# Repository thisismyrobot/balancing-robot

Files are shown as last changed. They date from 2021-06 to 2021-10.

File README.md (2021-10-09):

# Balancing robot

Using a BetaFlight-equipped flight controller (and later on an MPU6050) to
give the orientation and an Arduino Nano (and later an ESP32) for control.

End goal is the Wheelie Boy from The Peripheral.

This is an educational (for myself) project but I want to share my steps
towards achieving (or not) this goal.

If you want to try out some of the code, use the tags below, anything else is
probably WIP and may not do anything useful :)

## Version 4 (TODO/WIP)

### Thoughts

 * Will build a new chassis, with new motors, and target wheel size.
 * If encoders are high enough resolution I will retry the closed-loop
   control, if not will instead use the behaviour (ie oscillating, running
   away) to self tune a little.
 * Will move control board to bottom to simplify wiring and to stop instances
   where I tap the "head" back and forward while tuning from saturating the
   accelerometers which caused it to lose an accurate "zero" inclination.
 * Definitely using an MPU6050.

## Version 3

See [Tag 3.0](https://github.com/thisismyrobot/balancing-robot/releases/tag/3.0)

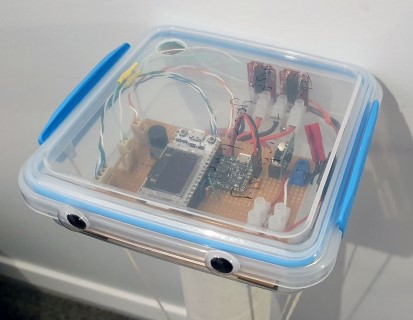
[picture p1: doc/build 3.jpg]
 

### Hardware

 * HappyModel SP Racing F3 EVO Brushed Micro FC - running BetaFlight 3.1.7 with minimal configuration except for fast serial response.
 * 2 x Solarbotics L293D Secret Motor Driver
 * Heltec Automation WiFi Kit 32 (an ESP32 board) for control
 * ~~2 x DG01D-E 48:1 DC motor w/wheel, 3-9V~~ 2 x 48.75:1 DC motor w/wheel, 3-12V (search for "Arduino DC Motor with Wheel and Rubber Tyres") + bodged-on encoders from DG01D-E, as the DG01D-E is just not powerful enough. Measurements suggest 1/3 of the power.
 * Pololu 5V, 2.5A Step-Down Voltage Regulator D24V22F5
 * 3S LiPo (450mAh 45C)

### Thoughts

Not a great success. Switching to an ESP32 was a good, but implementing
closed-loop motor control didn't improve motor speed accuracy as the encoder
counts per revolution were too low. As a consequence a slower PID loop
frequency was needed to ensure enough counts were taken to correct the speed,
but that introduced lag in response.

## Version 2

See [Tag 2.0](https://github.com/thisismyrobot/balancing-robot/releases/tag/2.0)

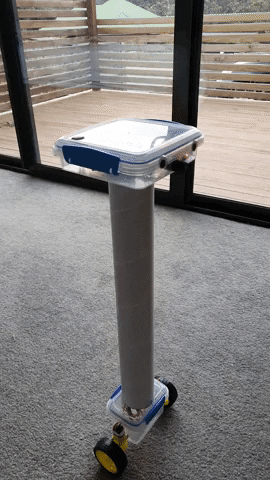
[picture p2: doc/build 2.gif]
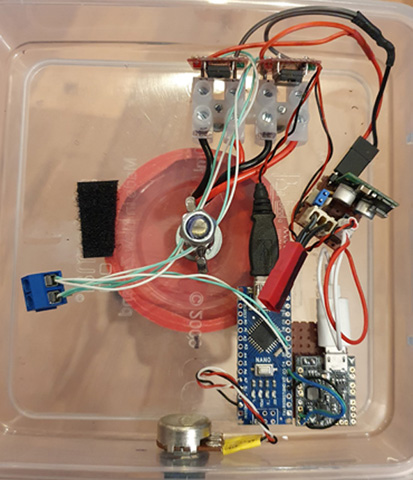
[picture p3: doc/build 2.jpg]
 

### Hardware

 * HappyModel SP Racing F3 EVO Brushed Micro FC - running BetaFlight 3.1.7
  with minimal configuration except for fast serial response.
 * 2 x Solarbotics L293D Secret Motor Driver
 * Arduino Nano
 * 2 x 48.75:1 DC motor w/wheel, 3-12V (search for "Arduino DC Motor with
   Wheel and Rubber Tyres")
 * Pololu 5V, 2.5A Step-Down Voltage Regulator D24V22F5
 * 3S LiPo (450mAh 45C)

### Thoughts

Pretty much balances. Next version will use encoders to get better motor speed
control and also distance measurement so I can start correcting for it
creeping.

## Version 1

See [Tag 1.0](https://github.com/thisismyrobot/balancing-robot/releases/tag/1.0)

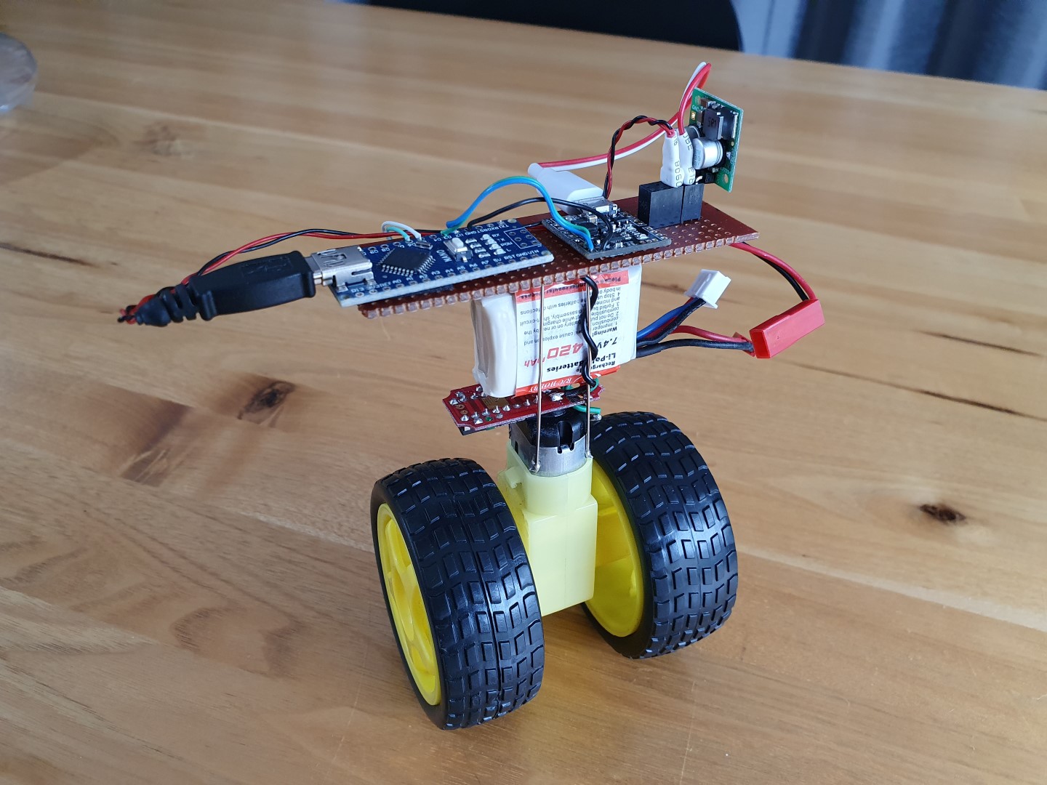
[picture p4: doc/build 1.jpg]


### Hardware

 * HappyModel SP Racing F3 EVO Brushed Micro FC - running BetaFlight 3.1.7
   with minimal configuration.
 * Solarbotics L293D Secret Motor Driver
 * Arduino Nano
 * 48.75:1 DC motor w/wheel, 3-12V (search for "Arduino DC Motor with Wheel
   and Rubber Tyres")
 * Pololu 5V, 2.5A Step-Down Voltage Regulator D24V22F5
 * 2S and 3S LiPos to test (3S better)

### Thoughts

Too short to even start tuning PID, but it was a good proof of concept of
using the drone controller for orientation.

# Some notes on motors

I am trying different motors as I progress and I'll log what I know about them
here, performance-wise.

| Motor model | Robot version(s) | Stall Torque | No Load Speed |
| --- | --- | --- | --- |
| DG01D-A130GEARMOTOR | 1 + 2 | 0.8kg/cm @ 4.5V | 180 RPM @ 4.5V |
| DG01D-E | 3? | 0.8kg/cm @ 4.5V | 180 RPM @ 4.5V |
| FS90R | 4? Wheelie Boy? | 1.3kg/cm @ 4.8V | 100 RPM @ 4.8V |

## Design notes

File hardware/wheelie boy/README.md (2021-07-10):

# Notes as I spec out the wheelie boy design from The Peripheral

https://app.milanote.com/1LZwqI1BNqTP8V?p=4gEVYU8Zxy4

## Font

Font is ToySans from: https://www.fontspace.com/category/toys-r-us

    license: Creative Commons (by-nc-nd) Attribution Non-commercial No Derivatives 
    link: https://www.fontspace.com/toysans-font-f22064

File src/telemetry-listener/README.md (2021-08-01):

# Telemetry Listener

Prints out telemetry from the robot, received over UDP.

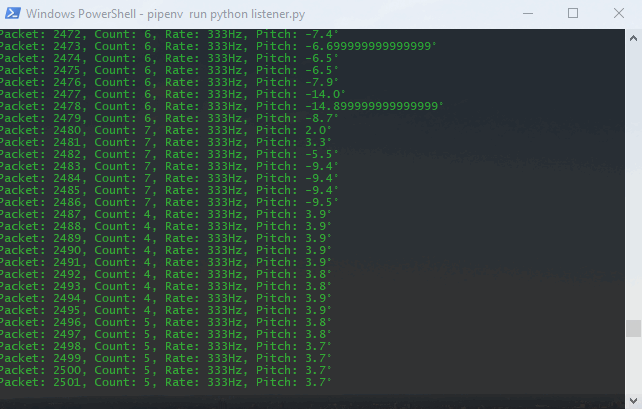
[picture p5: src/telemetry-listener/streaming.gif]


## PID tuning

An example application is the closed-loop motor control tuning I did using
data from the listener:

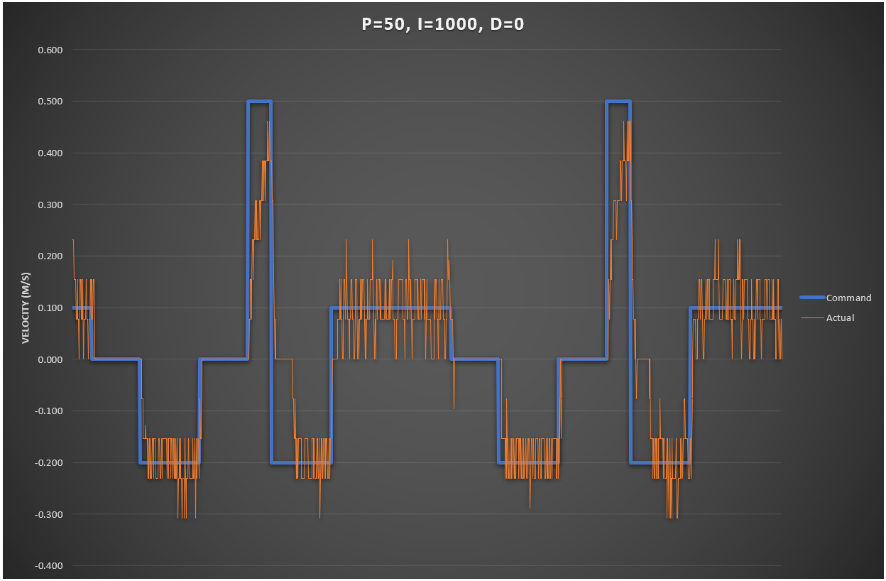
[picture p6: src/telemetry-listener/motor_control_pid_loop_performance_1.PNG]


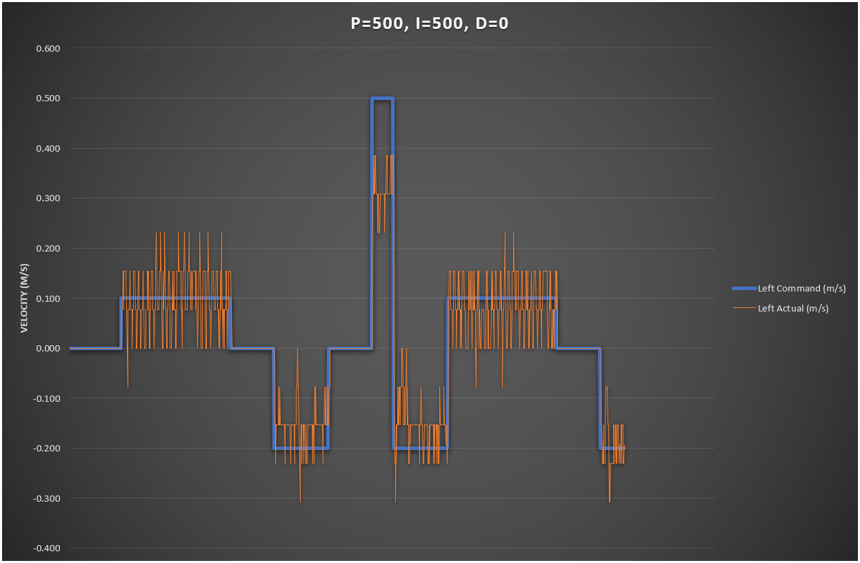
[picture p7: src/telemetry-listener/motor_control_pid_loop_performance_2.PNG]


## Install

    pip install pipenv
    pipenv install

## Run

    pipenv run python listener.py

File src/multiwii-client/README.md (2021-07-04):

Simple Python client to stream attitude data from a MultiWii serial device.

Built to find out how fast I could request data.

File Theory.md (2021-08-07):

# What (I think) makes a good balancing robot

Trying to describe this without a formula. It's close to correct but I will
keep updating as I learn more.

## Height/centre of mass/moment of inertia

Moving and concentrating mass towards the top of the robot will give the
control system more time to react to tipping and reduce the power requirements
of the motors to regain balance.

### Centre of Mass

The Centre of Mass of an object is the average position of the items within
it, weighted by their mass.

For the purposes of approximation, the Centre of Mass of our robot is it's
balance point along its length when laying on it's side.

## Torque Arm

When a solid object has a force put upon it, and that force is not directly
pointing at the Centre of Mass, the object will both move and be torqued
around the Centre of Mass. The line from the Centre of Mass to where the force
is acting is the Torque Arm. The longer the Torque Arm the greater the torque.
The greater the angle between the Torque Arm and the force, the more the force
will contribute to rotation and less to moving. 100% of the force will
contribute to rotation when the force is acting at 90 degrees to the Torque
Arm.

### Moment of Inertia

The Moment of Inertia of an object is its resistance to acceleration around a
pivot, based on its mass and the distribution of its mass compared to the
pivot. Adding mass to an object or moving an object's mass away from a pivot
will both increase the Moment of Inertia.

The greater the Moment of Inertia a mass has around a pivot, the more
resistant it will be to forces trying to accelerate its rotation around around
that pivot.

## Tipping

When the robot is stationary and starting to tip, it is because gravity is
applying a vertical force that is resulting in a torque around a pivot (its
wheel contact patches). The higher the Moment of Inertia is around the pivot,
the more slowly it will accelerate in rotation towards the ground.

The benefit of it more slowly accelerating is your control system has more
time to correct.

## Recovering

When a robot moves laterally to correct its balance, two forces are in play.

Firstly, the rotation of the wheels by the motor creates an opposite torque on
the robot that attempts to straighten it. The lighter the robot the more
impact this torque will have. The greater the Moment of Inertia of the robot
around the axle pivot, the less impact the torque will have.

This torque is not generally accounted for in your control system so the less
impact it has the better.

Secondly, the sideways motion of the base of the robot as it attempts to move
the wheels directly under the top is a lateral force on the bottom of the
robot that is attempting to torque the robot to vertical. The Torque Arm is
between the Centre of Mass and the wheel contact patches. Inhibiting this
torque will be the Moment of Inertia of that rotation around the Centre of
Mass. The higher up the robot the centre of mass is and/or the more
concentrated it is at the Centre of Mass (and thus the lower the Moment of
Inertia around the Centre of Mass pivot), the the less lateral force required
to torque the robot back to vertical.

This reduction in required lateral force reduces the power requirements of the
motors.

# Tuning approach

The usual, tune P, the I, then D. Some people say for balancing robots to go
with zero I, some go with I = 10x P. YMMV. D is nearly always a 100th or
1000th of P.

# Fast PID control loop time

I got now meaningful balancing performance before hitting over 150Hz loop
time (currently 192 Hz). At 10Hz it was hopeless.

I don't have a good external reference but 1ms loop times (so 1000Hz) are
successful in https://www.youtube.com/watch?v=TN6u-D992sw

# Constant PID control loop time

Using the standard Arduino PID library, variances in PID control loop time are
not taken into account which can impact D term. Keep it as constant as
possible.

# Battery voltage vs. P

Consider raising P by the drop (%) in battery voltage, and vice versa. Motor
voltage is proportional to motor speed so this will help maintain level
performance as a battery sags.

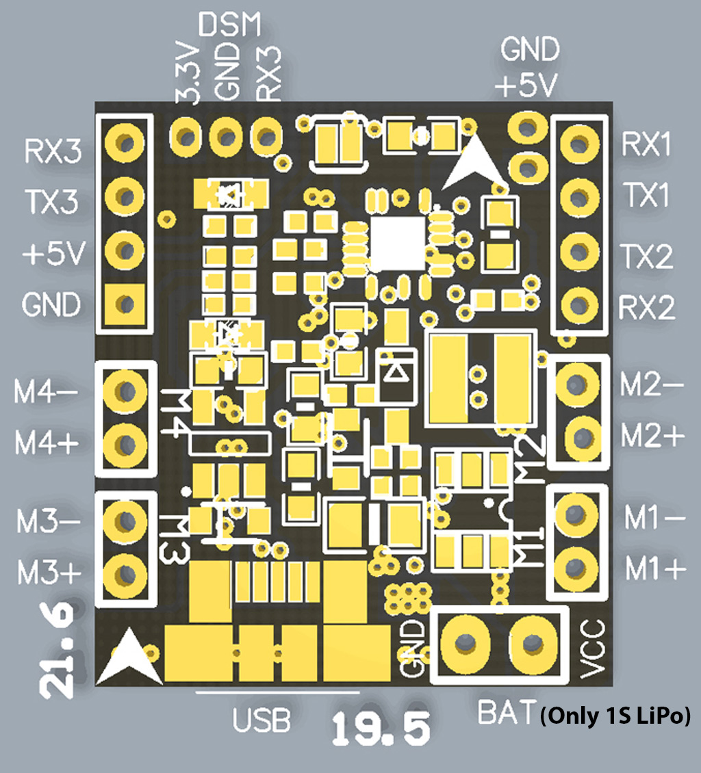
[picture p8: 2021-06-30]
hardware/HappyModel SP Racing F3 EVO Brushed Micro FC/happymodel-f3-evo-brushed-v2-big001.jpg

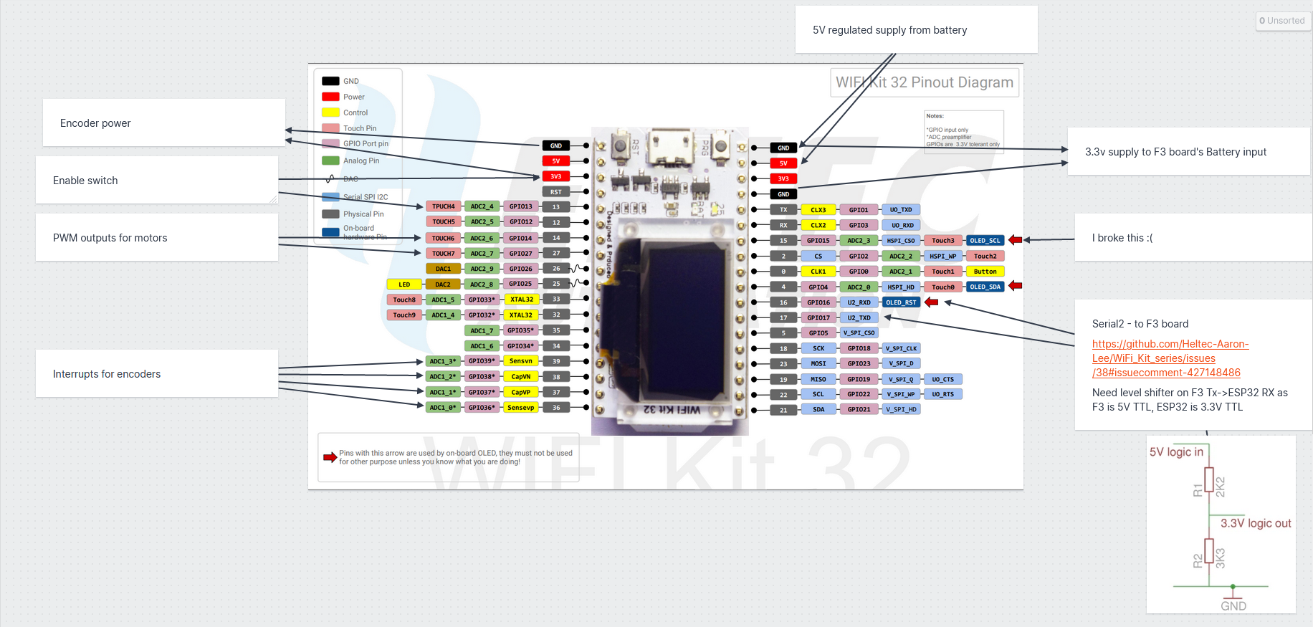
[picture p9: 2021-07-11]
hardware/Heltec WiFi Kit 32/Integration.PNG

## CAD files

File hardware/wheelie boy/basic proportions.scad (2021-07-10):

$fn = 50;

module rod(diameter, height) {
    color([1, 0, 0]) cylinder(h=height, r=diameter / 2);
}

module base(diameter) {
    color([1, 0, 0]) sphere(r=diameter / 2);
}

module screen(width, height, thickness) {
    color([0, 0, 0]) translate([-thickness / 2, -width / 2, 0]) cube([thickness, width, height]);
}

module wheel(width, diameter) {
    
    translate([0, 0, -width * 0.125]) cylinder(h=width * 0.25, r=(diameter / 2) - width);
    color([0.2, 0.2, 0.2]) rotate_extrude() translate([(diameter / 2) - (width / 2), 0, 0]) circle(r = width / 2);
}

ball_diam = 10;
rod_height = 35;
rod_diam = 1;

screen_height = ball_diam * 2;
screen_width = screen_height * (3/4);

base(ball_diam);
translate([0, 0, ball_diam / 2]) rod(rod_diam, rod_height);
translate([0, 0, rod_height + (ball_diam / 2)]) screen(screen_width, screen_height, 1);
translate([0, (ball_diam / 2)+1.5, 0]) rotate([-90, 0, 0]) wheel(ball_diam / 2.5, ball_diam * 1.2);
translate([0, -(ball_diam / 2)-1.5, 0]) rotate([90, 0, 0]) wheel(ball_diam / 2.5, ball_diam * 1.2);

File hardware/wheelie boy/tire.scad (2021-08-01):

use <Toysans-Xe5d.ttf>

print = false;

$fn = print ? 200 : 20;

hub_width = 26;
hub_diam = 51.6;

hubcap_thickness = 1;

spoke_width = 0.75; // Tune to single pass of nozzle.

rim_width = 2;
tire_diam = 110;
tire_width = 30;
    

module hub()
{
    cylinder(r=hub_diam / 2, h=hub_width);
}

module hubCap()
{
    color([0.5, 0.5, 0.5]) cylinder(r=hub_diam / 2, h=hubcap_thickness);
    
    font_size = hub_diam / 6;
    translate([0, 0, hubcap_thickness]) linear_extrude(hubcap_thickness) text("Wheelie", font_size, "ToySans", halign="center", spacing=1.1);    
    translate([0, -hub_diam / 4.5, hubcap_thickness]) linear_extrude(hubcap_thickness) text("Boy", font_size, "ToySans", halign="center", spacing = 1.1);    
}

module tire()
{
    // Inner rim.
    difference() {
        cylinder(r=(hub_diam / 2) + rim_width, h=tire_width);
        translate([0, 0, -10]) cylinder(r=hub_diam / 2, h=tire_width + 20);
    }

    // Inner rim.
    difference() {
        cylinder(r=(tire_diam / 2), h=tire_width);
        translate([0, 0, -10]) cylinder(r=(tire_diam / 2) - rim_width, h=tire_width + 20);
    }
   
    // Airless-ness (think Michelin "Uptis")
    length = ((tire_diam - hub_diam) / 2) - (rim_width * 1.5);
    spokes = 30;
    for ( i = [0 : spokes] )
    {
        rotate([0, 0, (360 / spokes) * i]) translate([(hub_diam / 2) + rim_width, 0, 0]) linear_extrude(tire_width) {
            polygon(points=[[-rim_width/2,-spoke_width/2],[length,-spoke_width/2],[length,spoke_width/2],[-rim_width/2,spoke_width/2]]);
        }
    }
}

if (!print) {
    hub();
    translate([0, 0, hub_width]) hubCap();
}
else {
    translate([0, ((tire_diam + hub_diam) / 2) + 10, 0]) hubCap();
}

color([0.5, 0.5, 0.5]) tire();

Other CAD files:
hardware/wheelie boy/old artwork/WheelieBoy.skp

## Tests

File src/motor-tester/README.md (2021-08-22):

# Some DC motor theory

For a DC motor receiving a rated voltage:

 - It will have a Stall Torque, and a rated (no-load) RPM
 - Torque reduces linearly from the Stall Torque at zero RPM to zero at the rated RPM
 - The peak power is at 1/2 of the Stall Torque - which is the same point as half the rated RPM

https://nrsyed.com/2018/01/21/how-to-read-a-dc-motor-datasheet/

That means you can estimate peak power by calculating the power with inputs of
1/2 the Stall Torque and 1/2 the rated no-load RPM.

## Units/constants

### f<sub>RPM</sub>

This is not a real unit, but I'm using it to make the formulas clearer to
understand - it is the RPM of the motor.

### P = Power (Watts)

### τ = Torque (Nm)

Can be calculated from kgf.cm using: τ = (kgf.cm * g) / 100

Can be converted to kgf.cm using: kgf.cm = (τ * 100) / g

### ω = Angular Velocity (Radians/second)

Can be calculated from RPM using: ω = 2π * (f<sub>RPM</sub> / 60)

### g = Gravity

9.80665

## Formulas

### P = τ * ω

Power from torque and angular velocity

### Estimated power

Populating from above components:

P = (τ<sub>stall</sub> / 2) * ((2π * (f<sub>RPM</sub> / 60)) / 2)

Simplified:

P = (π * f<sub>RPM</sub> * τ<sub>stall</sub>) / 120

#### Example

https://www.banggood.com/CHIHAI-MOTOR-DC12V-350rpm-Encoder-Motor-DC-Gear-Motor-with-Cover-p-1245484.html

Motor rated speed (f<sub>RPM</sub>): 11907rpm (after 34.02:1 gearbox)
Blocking (stall) torque (τ<sub>stall</sub>): 12kg.cm (which after 34.02:1 gearbox is 0.03459 Nm)

P = (π * f<sub>RPM</sub> * τ<sub>stall</sub>) / 120

  = (π * 11907 * 0.03459) / 120

  = 10.7 Watts @ 12V @ 5954 RPM

As compared to 8.5W on document?

## Experiments in measuring comparable motor performance

###  stall_torque_calculator.py - measuring stall torque per volt

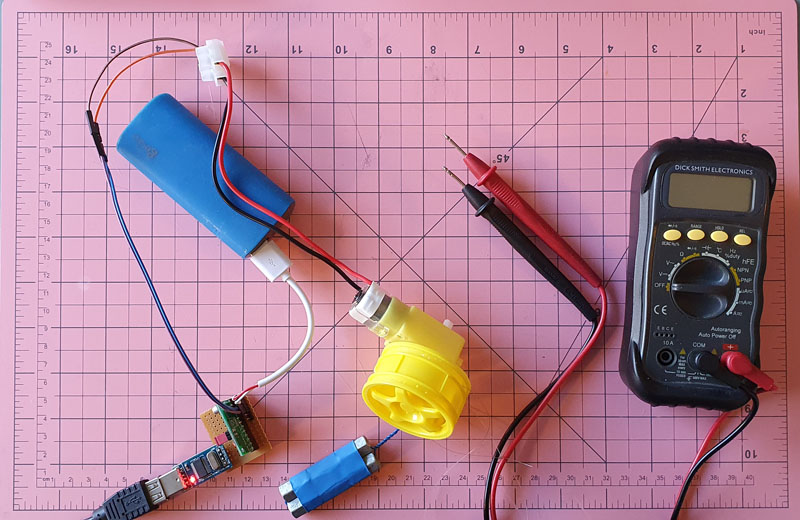
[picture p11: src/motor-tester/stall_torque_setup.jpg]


The idea is to ramp voltage until a weight starts to lift, then slow down
until it stops lifting, measure the voltage and use the mass and lifting wheel
diameter to determine the applied torque when it stalled.

Stall torque increases with voltage, fairly linearly, so we can apply the
ratio of the stall torque and voltage to estimate a stall torque per a spec
sheet volt value to compare motors by even if the voltage at which their stall
torque is specified at differs.

#### DG01D-A130GEARMOTOR

This motor + gearbox is spec'd to be 0.8kgf.cm @ 4.5V. As a ratio that is
0.17778 kgf.cm/V.

pipenv run python stall_torque_calculator.py --qik

    Mass of weight in kilograms (0.052):
    Wheel diameter in metres (0.0479):
    Supply voltage (5): 5.1
    Press [Enter] to begin...
    Press [Enter] when the motor starts!
    Press [Enter] when the motor stops!
    0.01Nm (0.12kgf.cm) @ 0.92V => 0.01328Nm/V (0.1354kgf.cm/V)

This is quite different to spec, but I think that the voltage was too far away
from the nominal, and more weight seems to improve the accuracy:

pipenv run python stall_torque_calculator.py --qik

    Mass of weight in kilograms (0.052): 0.16
    Wheel diameter in metres (0.0479):
    Supply voltage (5): 5.1
    Press [Enter] to begin...
    Press [Enter] when the motor starts!
    Press [Enter] when the motor stops!
    0.04Nm (0.38kgf.cm) @ 2.00V => 0.01879Nm/V (0.1916kgf.cm/V)

pipenv run python stall_torque_calculator.py --qik

    Mass of weight in kilograms (0.052): 0.284
    Wheel diameter in metres (0.0479):
    Supply voltage (5): 5.1
    Press [Enter] to begin...
    Press [Enter] when the motor starts!
    Press [Enter] when the motor stops!
    0.07Nm (0.68kgf.cm) @ 3.44V => 0.01939Nm/V (0.1977kgf.cm/V)

These two results are very close, despite a (~75% increase in weight), and
their average (0.19465) is pretty accurate, because 0.19465 * 4.5V =
0.875925kgf.cm and, as above, the spec says the stall torque is 0.8kgf.cm at
4.5V for this motor.

I think there is potential in this technique of estimating comparable stall
torque between different tested motors and spec sheets, as long as the stall
voltages are reasonable close.

#### DG01D-E

pipenv run python stall_torque_calculator.py --qik

    Mass of weight in kilograms (0.052):
    Wheel diameter in metres (0.0479):
    Supply voltage (5): 5.1
    Press [Enter] to begin...
    Press [Enter] when the motor starts!
    Press [Enter] when the motor stops!
    0.01Nm (0.12kgf.cm) @ 1.88V => 0.00650Nm/V (0.0662kgf.cm/V)

pipenv run python stall_torque_calculator.py --qik

    Mass of weight in kilograms (0.052): 0.09
    Wheel diameter in metres (0.0479):
    Supply voltage (5): 5.1
    Press [Enter] to begin...
    Press [Enter] when the motor starts!
    Press [Enter] when the motor stops!
    0.02Nm (0.22kgf.cm) @ 2.68V => 0.00789Nm/V (0.0804kgf.cm/V)

pipenv run python stall_torque_calculator.py --qik

    Mass of weight in kilograms (0.052): 0.162
    Wheel diameter in metres (0.0479):
    Supply voltage (5): 5.1
    Press [Enter] to begin...
    Press [Enter] when the motor starts!
    Press [Enter] when the motor stops!
    0.04Nm (0.39kgf.cm) @ 4.18V => 0.00910Nm/V (0.0928kgf.cm/V)

This backed up some of the results I had before, though the motor is soo weak
I had to use lower weights. On pure comparison though, the DG01D-E is has a
50% lower stall torque compared to the DG01D-A130GEARMOTOR. The below
measurements show it as having 1/3 of the power. No wonder it's not working
for V3 of this robot.

### tester.py - measuring motor power

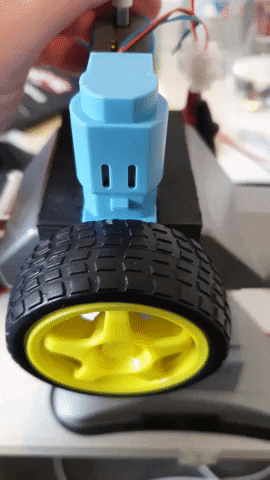
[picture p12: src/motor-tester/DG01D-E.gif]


This is a little simpler. By lifting a known weight a known distance over a
known time, using a known voltage, you can calculate the power in Watts of a
motor.

#### DG01D-A130GEARMOTOR

py tester.py

    Mass of weight in kilograms (0.05):
    Wheel diameter in metres (0.0665):
    Wheel rotations (2):
    Duration of lift in seconds: 0.65
    Battery voltage (5):
    0.02Nm (0.17kgf.cm) & 0.32W @ 5.0V & 184.62RPM

#### DG01D-E

py tester.py

    Mass of weight in kilograms (0.05):
    Wheel diameter in metres (0.0665):
    Wheel rotations (2): 1
    Duration of lift in seconds: 0.9666666666666667
    Battery voltage (5):
    0.02Nm (0.17kgf.cm) & 0.11W @ 5.0V & 62.07RPM

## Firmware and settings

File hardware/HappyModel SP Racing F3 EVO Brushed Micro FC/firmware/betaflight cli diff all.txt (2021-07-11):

# diff all
# Betaflight / SPRACINGF3EVO 3.1.7 Apr  3 2017 / 22:28:08 (e1c4b5c)
defaults

feature -VBAT
feature -CURRENT_METER
feature -RSSI_ADC
feature -BLACKBOX
feature -TRANSPONDER
feature -SDCARD
feature SOFTSERIAL
serial 0 1 115200 57600 0 115200
set serial_update_rate_hz = 1000
profile 0

rateprofile 0
rateprofile 0

rateprofile 1

rateprofile 2

rateprofile 0
profile 1

rateprofile 0
rateprofile 0

rateprofile 1

rateprofile 2

rateprofile 0
profile 2

rateprofile 0
rateprofile 0

rateprofile 1

rateprofile 2

rateprofile 0
profile 0
save

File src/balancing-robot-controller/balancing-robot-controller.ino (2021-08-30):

/*
 * Add https://dl.espressif.com/dl/package_esp32_index.json as an additional board manager URL.
 * Install esp32 board via the board manager (1.0.6).
 * Select Heltec_Wifi_Kit_32 as board.
 * 
 * Extra libraries:
 *  - MsgPack (0.3.8)
 *  - PID (1.2.0)
 *  - ESP32Encoder (0.5.1)
 * 
 */
#include <Arduino.h>
#include <HardwareSerial.h>
#include <PID_v1.h>
#include "src/telemetry.h"
#include "src/configuration.h"
#include "src/drive.h"

// Robot configuration and characteristics.
#define ANGLE_DEADZONE 0.1 // +/- this pitch value is considered zero.
#define ANGLE_FALLEN 40

// Closed loop motor control.
#define WHEEL_DISTANCE_M 0.208916  // 66.5mm diameter.
#define ENC_PULSES_PER_ROTATION 543.0  // 48:1 gearbox and ?!?! 11.3125 divisor. Odd.
#define MOTOR_CONTROL_P 50
#define MOTOR_CONTROL_I 1000
#define MOTOR_CONTROL_D 0

// Arduino wiring configuration.
#define ENABLE_GPIO 13
#define LED_GPIO 25

#define MOTOR_FORWARD_LEFT_GPIO 27
#define MOTOR_REVERSE_LEFT_GPIO 14
#define MOTOR_FORWARD_RIGHT_GPIO 26
#define MOTOR_REVERSE_RIGHT_GPIO 25

#define ENC_LEFT_A_GPIO 39
#define ENC_LEFT_B_GPIO 38
#define ENC_RIGHT_A_GPIO 36
#define ENC_RIGHT_B_GPIO 37

// PWM
#define PWM_FREQUENCY 5000
#define PWM_RESOLUTION 8
#define PWM_MOTOR_FORWARD_LEFT_CHANNEL 0
#define PWM_MOTOR_REVERSE_LEFT_CHANNEL 1
#define PWM_MOTOR_FORWARD_RIGHT_CHANNEL 2
#define PWM_MOTOR_REVERSE_RIGHT_CHANNEL 3

// Multi-Wii commands.
#define MSP_ATTITUDE 108

// PID configuration.
#define P 0.1
#define I 0.0
#define D 0.0

// PID instances.
double pitchPidSetpoint = 0;
double pitchPidInput;
double pitchPidOutput;
PID pitchPid(&pitchPidInput, &pitchPidOutput, &pitchPidSetpoint, P, I, D, DIRECT);

// Motor commands and tracking
double leftSpeedCommand = 0;
double rightSpeedCommand = 0;
double leftSpeedActual = 0;
double rightSpeedActual = 0;

// Statistics/telemetry
int watchdog = 0;
int rate = 0;
const int statsUpdateMillis = 250;
unsigned long lastStatsUpdateMillis = 0;
int rateLoops = 0;

// Subtracted from sensor reading to get robot balanced = 0.
double pitchCorrection = 0;

// Pointers to the shared data for telemetry and configuration.
TelemetryData_t telemetryData = {
    &watchdog,
    &rate,
    &pitchCorrection,
    &pitchPidInput,
    &pitchPidOutput,
    &leftSpeedCommand,
    &rightSpeedCommand,
    &leftSpeedActual,
    &rightSpeedActual    
};

Configuration_t configuration = {
    &pitchCorrection
};

DriveCommands_t driveCommands = {
    &leftSpeedCommand,
    &rightSpeedCommand,
    &leftSpeedActual,
    &rightSpeedActual
};

HardwareSerial F3Serial(1);

void setup() {
    setupPins();
    setDriveParams(
        PWM_MOTOR_FORWARD_LEFT_CHANNEL,
        PWM_MOTOR_REVERSE_LEFT_CHANNEL,
        PWM_MOTOR_FORWARD_RIGHT_CHANNEL,
        PWM_MOTOR_REVERSE_RIGHT_CHANNEL,
        ENC_LEFT_A_GPIO,
        ENC_LEFT_B_GPIO,
        ENC_RIGHT_A_GPIO,
        ENC_RIGHT_B_GPIO,
        WHEEL_DISTANCE_M,
        ENC_PULSES_PER_ROTATION,
        MOTOR_CONTROL_P,
        MOTOR_CONTROL_I,
        MOTOR_CONTROL_D);

    pitchPid.SetOutputLimits(-1.0, 1.0);
    pitchPid.SetMode(AUTOMATIC);

    while(!enabled()) {
        digitalWrite(LED_GPIO, LOW);
        delay(250);
        digitalWrite(LED_GPIO, HIGH);
        delay(250);
    }

    setupF3();
    pitchCorrection = getAveragePitch(20, 200);

    startConfigurationTask((Configuration_t *)&configuration);
    startTelemetryTask((TelemetryData_t *)&telemetryData);
    startDriveTask((DriveCommands_t *)&driveCommands);
}

double getAveragePitch(int loops, int delayMs)
{
    double average = 0;
    for(int i = 0; i < loops; i++)
    {
        average += readPitch();
        digitalWrite(LED_GPIO, LOW);
        delay(delayMs / 2);
        digitalWrite(LED_GPIO, HIGH);
        delay(delayMs / 2);
    }
    return average / loops;
}

void loop() {

    double pitch = readPitch();

    if (pitch > ANGLE_FALLEN || pitch < -ANGLE_FALLEN) {
        reset();
    }

    if (abs(pitch) <= ANGLE_DEADZONE) {
        pitch = 0;
    }

    pitchPidInput = -pitch;

    pitchPid.Compute();

    // Until steering implemented. - min +/- 0.1m/s
    leftSpeedCommand = pitchPidOutput;
    rightSpeedCommand = pitchPidOutput;

    updateStats();

    if(!enabled()) {
        reset();
    }
}

void setupPins() {
    pinMode(ENABLE_GPIO, INPUT_PULLDOWN);

    pinMode(LED_GPIO, OUTPUT);
    digitalWrite(LED_GPIO, LOW);

    ledcSetup(PWM_MOTOR_FORWARD_LEFT_CHANNEL, PWM_FREQUENCY, PWM_RESOLUTION);
    ledcSetup(PWM_MOTOR_REVERSE_LEFT_CHANNEL, PWM_FREQUENCY, PWM_RESOLUTION);
    ledcAttachPin(MOTOR_FORWARD_LEFT_GPIO, PWM_MOTOR_FORWARD_LEFT_CHANNEL);
    ledcAttachPin(MOTOR_REVERSE_LEFT_GPIO, PWM_MOTOR_REVERSE_LEFT_CHANNEL);
    ledcWrite(PWM_MOTOR_FORWARD_LEFT_CHANNEL, 0);
    ledcWrite(PWM_MOTOR_REVERSE_LEFT_CHANNEL, 0);

    ledcSetup(PWM_MOTOR_FORWARD_RIGHT_CHANNEL, PWM_FREQUENCY, PWM_RESOLUTION);
    ledcSetup(PWM_MOTOR_REVERSE_RIGHT_CHANNEL, PWM_FREQUENCY, PWM_RESOLUTION);
    ledcAttachPin(MOTOR_FORWARD_RIGHT_GPIO, PWM_MOTOR_FORWARD_RIGHT_CHANNEL);
    ledcAttachPin(MOTOR_REVERSE_RIGHT_GPIO, PWM_MOTOR_REVERSE_RIGHT_CHANNEL);
    ledcWrite(PWM_MOTOR_FORWARD_RIGHT_CHANNEL, 0);
    ledcWrite(PWM_MOTOR_REVERSE_RIGHT_CHANNEL, 0);
}

void setupF3() {
    delay(5000);

    // using UART2 pins.
    F3Serial.begin(115200, SERIAL_8N1, 16, 17);
}

void updateStats() {
    unsigned long nowMillis = millis();
    unsigned long elapsedMillis = nowMillis - lastStatsUpdateMillis;
    if (elapsedMillis > statsUpdateMillis) {
        watchdog++;
        rate = rateLoops / (elapsedMillis / 1000.0);
        rateLoops = 0;
        lastStatsUpdateMillis = nowMillis;
    }

    rateLoops++;
}

// Return a relative pitch, accounting for the configured balance point offset.
double readPitch() {

    // Request Attitude
    uint8_t cmd = MSP_ATTITUDE;
    uint8_t n_bytes = 0;
    uint8_t checksum = 0;

    F3Serial.write((byte *) "$M<", 3);
    F3Serial.write(n_bytes);
    checksum ^= n_bytes;

    F3Serial.write(cmd);
    checksum ^= cmd;

    F3Serial.write(checksum);
    F3Serial.flush(true);  // true = TX only.
    delay(2);

    // Read response    
    byte count = 0;

    int16_t roll = 0;
    int16_t pitch = 0;
    int16_t yaw = 0;

    // Descard everything until next '$'
    while (F3Serial.peek() != '$') {
        F3Serial.read();
    }

    // Full altitude message is 12 bytes.
    while(F3Serial.available() < 9);

    // Read the rest.
    while (F3Serial.available()) {
        count += 1;
        byte c = F3Serial.read();
        switch (count) {
            case 6:
                roll = c;
                break;
            case 7:
                roll <<= 8;
                roll += c;
                roll = (roll & 0xFF00) >> 8 | (roll & 0x00FF) << 8; // Reverse the order of bytes
                break;
            case 8:
                pitch = c;
                break;
            case 9:
                pitch <<= 8;
                pitch += c;
                pitch = (pitch & 0xFF00) >> 8 | (pitch & 0x00FF) << 8; // Reverse the order of bytes
                break;
            case 10:
                yaw = c;
                break;
            case 11:
                yaw <<= 8;
                yaw += c;
                yaw = (yaw & 0xFF00) >> 8 | (yaw & 0x00FF) << 8; // Reverse the order of bytes
                break;
        }
    }

    return (pitch / 10.0) - pitchCorrection;
}

void reset()
{
    ESP.restart();
}

bool enabled()
{
    return digitalRead(ENABLE_GPIO);
}

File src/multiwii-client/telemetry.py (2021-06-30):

import datetime
import time

import multiwii


def stream(port, baud, duration=None):
    results = 0
    start = None
    if duration is not None:
        duration = datetime.timedelta(seconds=duration)

    board = multiwii.MultiWii(port, baud)
    while True:
        if start is None:
            start = datetime.datetime.now()

        actual_duration = datetime.datetime.now() - start
        if duration is not None and actual_duration > duration:
            print(f'{results} results in {actual_duration.total_seconds()} = {(results / actual_duration.total_seconds())} Hz')
            break

        data = board.getData(multiwii.MultiWii.ATTITUDE)
        #print(data)
        if data is not None:
            results += 1


if __name__ == '__main__':
    stream('COM4', 38400, 10)

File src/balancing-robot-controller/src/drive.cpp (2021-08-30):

#include <Arduino.h>
#include <ESP32Encoder.h>
#include <PID_v1.h>
#include "drive.h"

double _driveP;
double _driveI;
double _driveD;

ESP32Encoder _encoderLeft;
ESP32Encoder _encoderRight;

int _forwardLeftPwmChannel = 0;
int _reverseLeftPwmChannel = 1;
int _forwardRightPwmChannel = 2;
int _reverseRightPwmChannel = 3;
double _wheelDistanceM;
double _pulsesPerRevolution;

// The drive task runs on the non-default core 0.
TaskHandle_t _DriveCoreZeroTask;

void setDriveParams(
    int forwardLeftPwmChannel,
    int reverseLeftPwmChannel,
    int forwardRightPwmChannel,
    int reverseRightPwmChannel,
    int encLeftAGpio,
    int encLeftBGpio,
    int encRightAGpio,
    int encRightBGpio,
    double wheelDistanceM,
    double pulsesPerRevolution,
    double p,
    double i,
    double d)
{
    _forwardLeftPwmChannel = forwardLeftPwmChannel;
    _reverseLeftPwmChannel = reverseLeftPwmChannel;
    _forwardRightPwmChannel = forwardRightPwmChannel;
    _reverseRightPwmChannel = reverseRightPwmChannel;
    _wheelDistanceM = wheelDistanceM;
    _pulsesPerRevolution = pulsesPerRevolution;
    _driveP = p;
    _driveI = i;
    _driveD = d;

    _encoderLeft.attachFullQuad(encLeftAGpio, encLeftBGpio);
    _encoderRight.attachFullQuad(encRightAGpio, encRightBGpio);
}


void startDriveTask(DriveCommands_t *driveCommands) {
    xTaskCreatePinnedToCore(
        _drive,                             /* Task function. */
        "Drive",                            /* name of task. */
        10000,                                        /* Stack size of task */
        (void *)driveCommands,        /* parameter of the task */
        1,                                                /* priority of the task */
        &_DriveCoreZeroTask,    /* Task handle to keep track of created task */
        0);                                             /* pin task to core 0 */
}


void _drive(void *parameters) {

    DriveCommands_t drive = *((DriveCommands_t*)parameters);

    double leftPwmOutput = 0;
    double rightPwmOutput = 0;

    PID leftPid(drive.leftSpeedActual, &leftPwmOutput, drive.leftSpeedCommand, _driveP, _driveI, _driveD, DIRECT);
    PID rightPid(drive.rightSpeedActual, &rightPwmOutput, drive.rightSpeedCommand, _driveP, _driveI, _driveD, DIRECT);

    leftPid.SetOutputLimits(-255, 255);
    rightPid.SetOutputLimits(-255, 255);
    leftPid.SetMode(AUTOMATIC);
    rightPid.SetMode(AUTOMATIC);

    unsigned long lastPidUpdateMillis = 0;
    int lastLeftCount = 0;
    int lastRightCount = 0;

    for(;;){

        unsigned long nowMillis = millis();
        double elapsedSeconds = (nowMillis - lastPidUpdateMillis) / 1000.0;

        int leftCount = (int32_t)_encoderLeft.getCount();
        int rightCount = (int32_t)_encoderRight.getCount();

        *drive.leftSpeedActual = _toDistanceMetres(leftCount - lastLeftCount) / elapsedSeconds;
        *drive.rightSpeedActual = _toDistanceMetres(rightCount - lastRightCount) / elapsedSeconds;

        leftPid.Compute();
        rightPid.Compute();

        _setPwm(leftPwmOutput, rightPwmOutput);

        lastPidUpdateMillis = nowMillis;
        lastLeftCount = leftCount;
        lastRightCount = rightCount;

        delay(100);  // 10Hz okay
    }
}


void _setPwm(double leftPwmVector, double rightPwmVector)
{
    double leftPwm = constrain(leftPwmVector, -255, 255);
    double rightPwm = constrain(rightPwmVector, -255, 255);

    int forwardLeftValue = 0;
    int reverseLeftValue = 0;
    int forwardRightValue = 0;
    int reverseRightValue = 0;

    if (leftPwm > 0) {
        forwardLeftValue = _map(leftPwm, 0, 255, 40, 255);
    } 
    else if (leftPwm < 0){
        leftPwm = -leftPwm;
        reverseLeftValue = _map(leftPwm, 0, 255, 40, 255);
    }

    if (rightPwm > 0) {
        forwardRightValue = _map(rightPwm, 0, 255, 45, 255);
    } 
    else if (rightPwm < 0){
        rightPwm = -rightPwm;
        reverseRightValue = _map(rightPwm, 0, 255, 45, 255);
    }

    ledcWrite(_forwardLeftPwmChannel, forwardLeftValue);
    ledcWrite(_reverseLeftPwmChannel, reverseLeftValue);
    ledcWrite(_forwardRightPwmChannel, forwardRightValue);
    ledcWrite(_reverseRightPwmChannel, reverseRightValue);
}

double _toDistanceMetres(double count)
{
    return (count / _pulsesPerRevolution) * _wheelDistanceM;
}

// Arduino built-in map is integer only.
double _map(double x, double in_min, double in_max, double out_min, double out_max) {
    return (x - in_min) * (out_max - out_min) / (in_max - in_min) + out_min;
}

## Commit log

2021-05-23 Working reading of MSP!
    [betaflight cli diff all.txt]
2021-05-24 led error output
2021-05-24 Mapped to cover deadspot in motor
2021-05-29 Lots of tweaks and waaaay closer to balancing
    [betaflight cli diff all.txt]
2021-05-29 Increased serial update rate and baud
    [betaflight cli diff all.txt]
2021-05-30 Fixed upper voltage bound
2021-06-06 A lot of tuning and tweaks to improve performance across the board
2021-06-30 Circuit pic
    (cherry picked from commit 2c9e6c4a0be2614cdea1b6a9f5a30ca77b9cfc02)
2021-06-30 Restructured folders
    [betaflight cli diff all.txt]
2021-07-03 Some scratchings to get an idea of the size/proportions of the wheelie boy
    And some old artwork from a previous crack at designing a static model
    [WheelieBoy.skp, basic proportions.scad]
2021-07-04 A massive amount of renaming and moving
    [betaflight cli diff all.txt]
2021-07-04 Untested ESP32 program for streaming telemetry on second core
2021-07-04 Motor notes
2021-07-10 Basic tire model
    [tire.scad]
2021-07-10 Fixed up font
    [tire.scad, tire.stl]
2021-07-10 tread, tweaks and made it less wide
    [tire.scad]
2021-07-10 Updated STL
2021-07-11 Test code that streams pitch and count
2021-07-11 working 333hz loop reading orientation
    [betaflight cli diff all.txt]
2021-07-11 Added enable button and led indication
    Also replaced incorrect manuals
    [balancing-robot-controller.ino]
2021-07-18 Moved config to cpp file
    [configuration.h]
2021-07-23 Tuned it pretty well for the DG01D-E motor pair
2021-07-24 Basic calculator of motor performance
2021-07-24 Fixed a lot :D
    [tester.py]
2021-07-24 Test runs from the slower new motor
2021-07-31 Prep for some PID tuning of the motor loop
2021-08-01 Tuned the motors control PID to be good enough
2021-08-01 Rough tune for new velocity-based pid loop
2021-08-01 Simplified wheel inspired a little from the Michelin Uptis
    [tire.scad]
2021-08-01 New STL
2021-08-01 Tweaked to get spokes to print
    [tire.scad]
2021-08-01 Stall torque per volt calculator
    [stall_torque_calculator.py]
2021-08-07 Working stall measuring, but I think I need both directions
    [stall_torque_calculator.py]
2021-08-08 PWM for estimation is better as that's the target
    I have to assume spec sheets are using supply voltage not the pulled
    down voltage due to load, and the PWM ratio across the supply
    voltage is the closest I can get to that.
2021-08-08 DG01D-E stall torque measurements
2021-08-17 Fixing some serious maths mistakes :(
    [tester.py]
2021-08-22 Untested right motor autonomy
2021-08-30 pins fixed to match split control
    [balancing-robot-controller.ino]
2021-08-30 Improved, including fixing some bias in the right wheel
    [balancing-robot-controller.ino, drive.cpp]
2021-08-30 Having some tuning issues. It's not currently better than without encoder.
    [balancing-robot-controller.ino, drive.cpp]
